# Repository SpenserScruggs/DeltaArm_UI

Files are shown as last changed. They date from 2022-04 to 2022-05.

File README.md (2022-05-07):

# DeltaArm_UI
  The goal of this project was to create a robotic arm that could track mouse movements and physically write them out on paper. Its purpose was to make signing large amounts of physical documents easier by recording a signature and then replaying it as many times as necessary. The project also exists as just a fun item to build and design and to help introduce people to robotics and electro-mechanical systems.

  This project includes the code for a graphical user interface made using WPF, Arduino code to interface with the computer, files for both the 3D printed parts and laser cut parts, MATLAB code to model the kinematic system, a bill of materials to list each part required with both their quantity and an Amazon link to purchase the part listed if applicable, and a manufacturing plan to give step by step instructions for assembly.

Final Product:


**Prototype Render:**
Untitled Project 15

**Prototype Functioning:**
https://user-images.githubusercontent.com/78044374/164074046-c8909eee-885d-474c-8c80-e7db3166021f.mov

**Record Feature:**
https://user-images.githubusercontent.com/78044374/164074614-67ea297b-0f7b-4717-87f8-4b7f0d07ca0b.mov

**MATLAB Code for Inverse Kinematics Solution:**
https://github.com/SpenserScruggs/DeltaArm_UI/blob/master/invKin.m

Code describes delta robot arms through 3 loop closure equations. Each loop closure equation is transformed from cartesian to a servo angle. Transformed loop closure equations are then trigonometrically substituted. Trig subbed equations are then solved with the quadratic formula and 2 solutions are given for every equation one solution with arms kinked in and one with arms kinked out. The kinked-out solution is selected through a sorting loop that chooses the smaller servo position thus selecting the preferred solution. From there the selected solutions from each loop closure solution is combined into an array and returned.

**AutoCAD files for frame of arm:**
https://github.com/SpenserScruggs/DeltaArm_UI/tree/master/AutoCAD%20Drawings

  Folder Contains all of the AutoCAD drawings that are needed for the frame of the arm. 

**BOM File:**
https://github.com/SpenserScruggs/DeltaArm_UI/blob/master/BOM.xlsx

  File contains all components needed for creation of the arm, as well as the prices, size, mass, and location of purchase of the components.

**Manufacturing Plan:**
https://github.com/SpenserScruggs/DeltaArm_UI/blob/master/Manufacturing%20Plan.docx

  Document provides step by step instructions for how to assemble the project.

**GUI Application:**
https://github.com/SpenserScruggs/DeltaArm_UI/tree/master/DeltaArm_UI

  This folder contains the C# and xaml code necessary to make the GUI and run the application (only works on Windows). To run it right click on the folder and select open with, then open with visual studio. Additionally if you only want the application/ don’t want to download visual studio you can download the executable directly here at: https://github.com/SpenserScruggs/DeltaArm_UI/blob/master/DeltaArm_UI.exe

**Circuit Diagram:**
https://github.com/SpenserScruggs/DeltaArm_UI/blob/master/Circuit_Diagram.png
  
  Circuit Diagram for the arduino and power supply

**Arduino Code:**
https://github.com/SpenserScruggs/DeltaArm_UI/blob/master/GUIKinematics2.ino

  Code that passes the xyz positions to the kinematic equations which can be converted to servo positions

**Source for the kinematic equations:**
https://hypertriangle.com/~alex/delta-robot-tutorial/

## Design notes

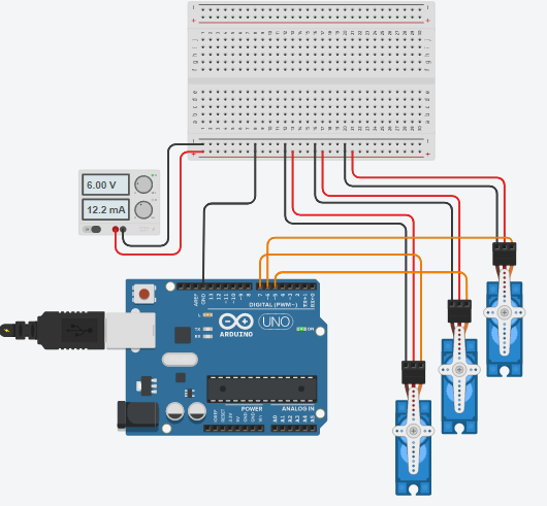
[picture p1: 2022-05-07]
Circuit_Diagram.png

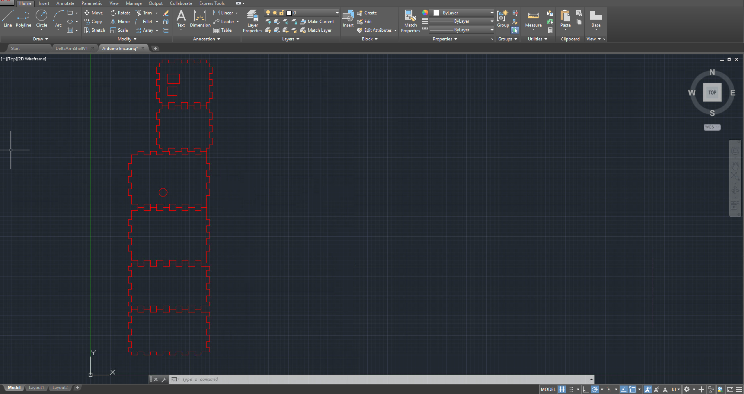
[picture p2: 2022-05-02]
AutoCAD Drawings/Arduino Casing Preview.PNG

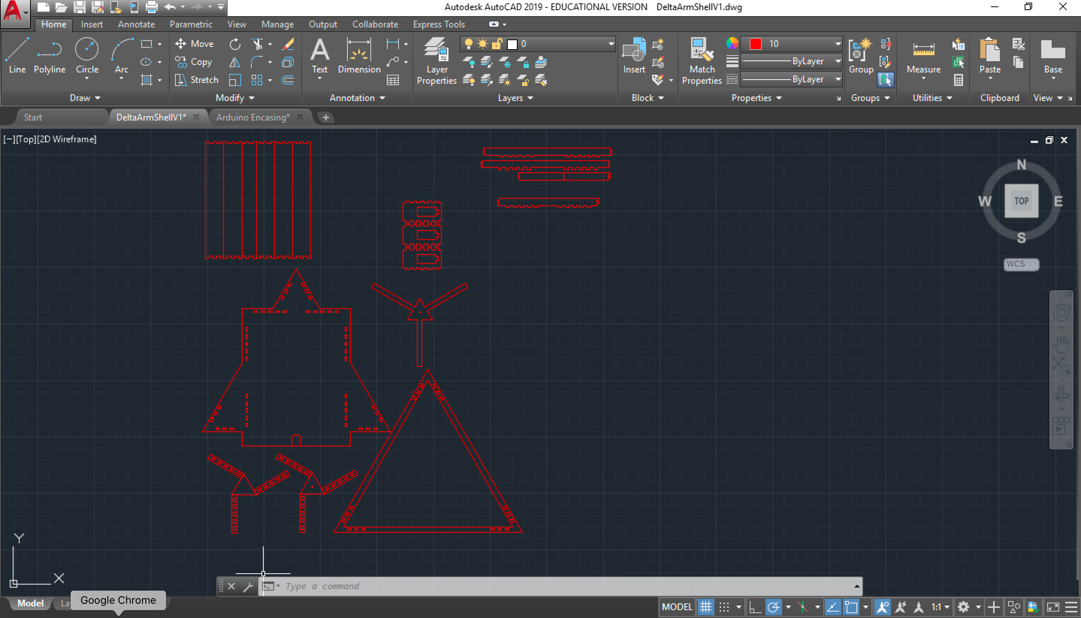
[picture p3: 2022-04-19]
AutoCAD Drawings/DeltaArmShellV1 Preview.png

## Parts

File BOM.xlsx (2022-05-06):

part_number | Part Name | Thumbnail Image | Custom Part | part_class | synopsis | revision | manufacturer_name | manufacturer_part_number | seller | link | unit_cost | Quantity | Total Cost | Mass (g) | Thickness (in)
1 | Servo Motor |  | FALSE | Servo | 180 degree servo with 12kg/cm torque | 0 | Deegoo-FPV | B07NQJ1VZ2 | Amazon | https://www.amazon.com/Control-Angle180-Digital-Torque-Helicopter/dp/B07NQJ1VZ2 | $5.50 | 3 | $16.49 | N/A | N/A
2 | Ball Joint |  | FALSE | Joint | Ball joint linkage | 0 | Uxcell | ‎A18122800ux0757 | Amazon | https://www.amazon.com/dp/B07Q2QSS72?psc=1&ref=ppx_yo2ov_dt_b_product_details | 0.9991666667 | 12 | 11.99 | N/A | N/A
3 | PSU |  | FALSE | PSU | Power supply for the servos | 0 | ‎ShenZhen ZuoEn Technologies Co. Ltd | ‎ISP-NW-PS-6V-WP-UL-12W | Amazon | https://www.amazon.com/dp/B01GCI99OG?ref=ppx_yo2ov_dt_b_product_details&th=1 | 6.29 | 1 | 6.29 | N/A | N/A
4 | Pen Pad |  | FALSE | Pen Pad | Pen control on windows computers | 0 | HUION | H430P-OTG | Amazon | https://www.amazon.com/gp/product/B078GZFY1C/ref=ppx_yo_dt_b_asin_title_o00_s00?ie=UTF8&psc=1 | 32.99 | 1 | 32.99 | N/A | N/A
5 | Lever |  | TRUE | 3D-Printed | Lever that connects servo with the arms | 1 | N/A | N/A | N/A | N/A | N/A | 3 | N/A | 6 | N/A
6 | Effector |  | TRUE | 3D-Printed | End effector that holds the pen | 2 | N/A | N/A | N/A | N/A | N/A | 1 | N/A | 3 | N/A
7 | Cap |  | TRUE | 3D-Printed | End cap for the top of the pen | 0 | N/A | N/A | N/A | N/A | N/A | 1 | N/A | 1 | N/A
8 | Lever Cap |  | TRUE | 3D-Printed | Screw cap for the lever | 0 | N/A | N/A | N/A | N/A | N/A | 6 | N/A | 1 | N/A
9 | Connector |  | TRUE | 3D-Printed | Connects the end effector with the joints | 1 | N/A | N/A | N/A | N/A | N/A | 3 | N/A | 1 | N/A
10 | Rod |  | TRUE | 3D-Printed | Connects the joints together | 1 | N/A | N/A | N/A | N/A | N/A | 6 | N/A | 4 | N/A
11 | Base Triangle |  | TRUE | Lazer-Cut | Holds the paper and side supports for arm | 0 | N/A | N/A | N/A | N/A | N/A | 1 | N/A | 900 | 1/4"
12 | TopTriangle |  | TRUE | Lazer-Cut | Holds main support for servos | 0 | N/A | N/A | N/A | N/A | N/A | 1 | N/A | 200 | 1/4"
13 | Top Support |  | TRUE | Lazer-Cut | Support for top of servos | 1 | N/A | N/A | N/A | N/A | N/A | 1 | N/A | 50 | 1/4"
14 | Bottom Support |  | TRUE | Lazer-Cut | Support for bottom of servos | 1 | N/A | N/A | N/A | N/A | N/A | 1 | N/A | 30 | 1/4"
15 | Main Support |  | TRUE | Lazer-Cut | Suspends servos above the base triangle | 0 | N/A | N/A | N/A | N/A | N/A | 1 | N/A | 30 | 1/4"
16 | Plexiglass Stands |  | TRUE | Lazer-Cut | Holds the top triangle above the base triangle | 0 | N/A | N/A | N/A | N/A | N/A | 6 | N/A | 40 | 1/8"
17 | Servo Brackets |  | TRUE | Lazer-Cut | Holds servos in place | 1 | N/A | N/A | N/A | N/A | N/A | 3 | N/A | 15 | 1/8"
18 | Arduino Box |  | TRUE | Lazer-Cut | Encloses Arduino and PCB board | 0 | N/A | N/A | N/A | N/A | N/A | 1 | N/A | 60 | 1/8"
19 | Paper Keepers |  | TRUE | Lazer-Cut | Holds paper in place on base platform | 3 | N/A | N/A | N/A | N/A | N/A | 1 | N/A | 30 | 1/8"

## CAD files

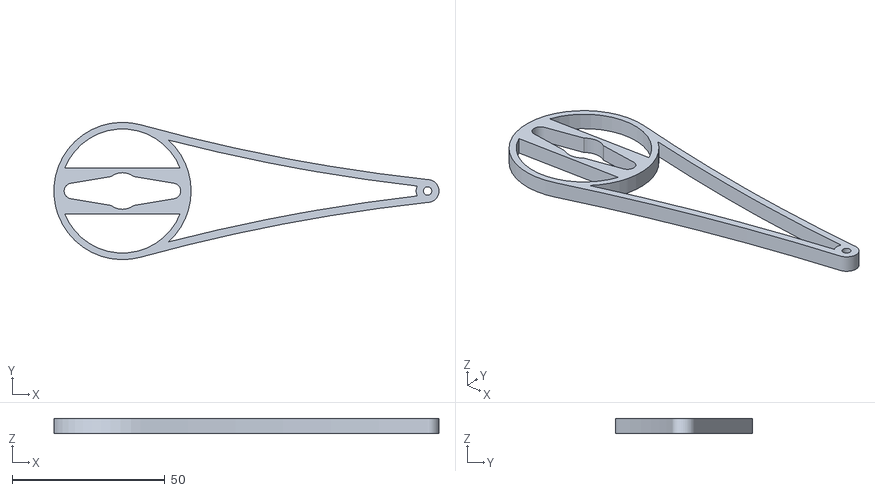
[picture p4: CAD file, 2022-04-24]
Stl_Files/lever.STL
126.2 x 45.0 x 5.00

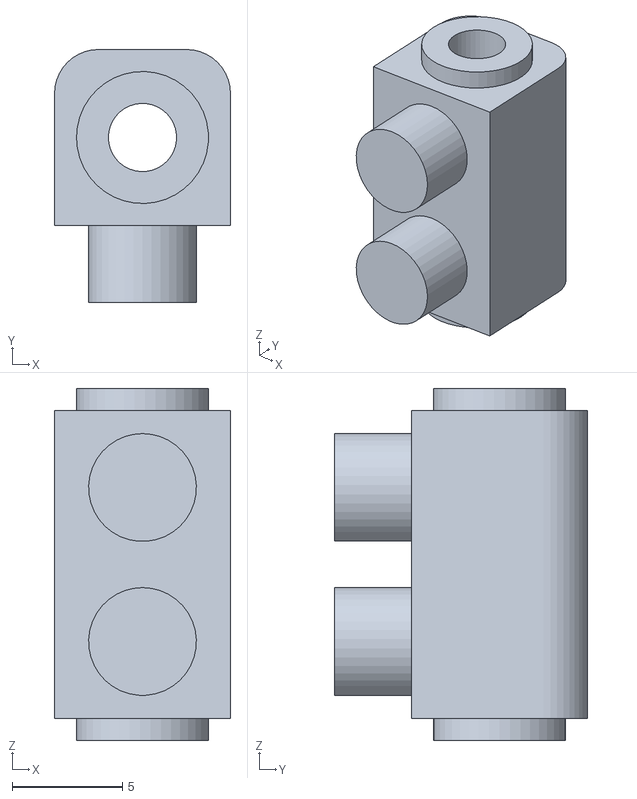
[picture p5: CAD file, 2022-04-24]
Stl_Files/connector.STL
8.00 x 11.5 x 16.0

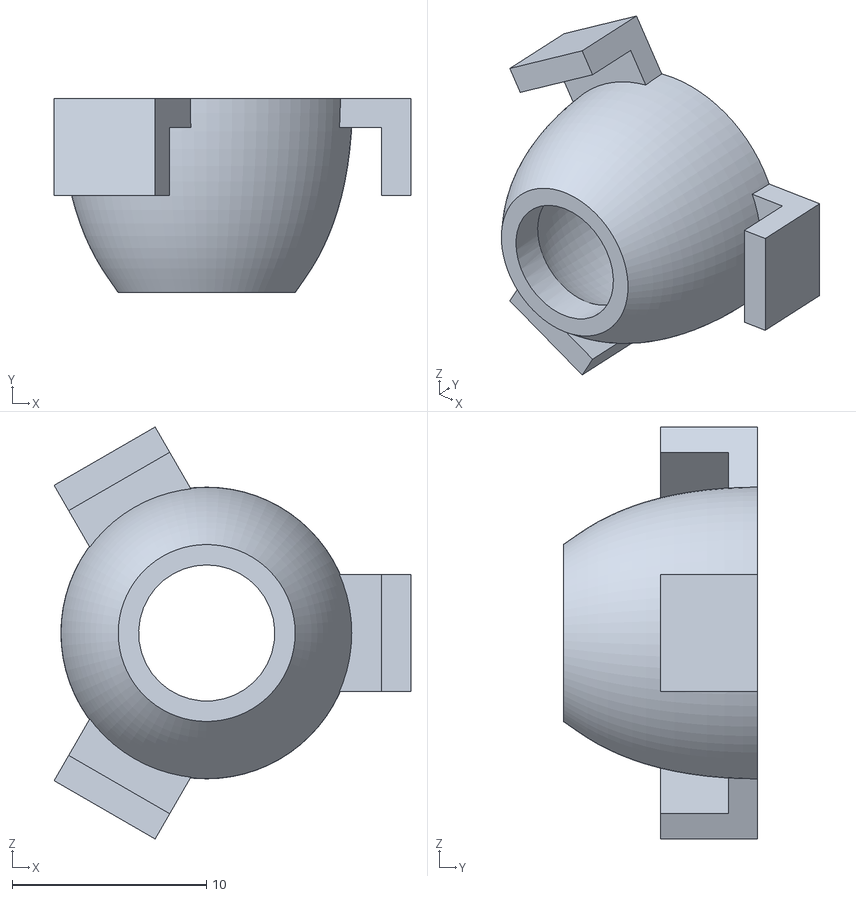
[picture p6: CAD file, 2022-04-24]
Stl_Files/cap.STL
18.3 x 10.0 x 21.2

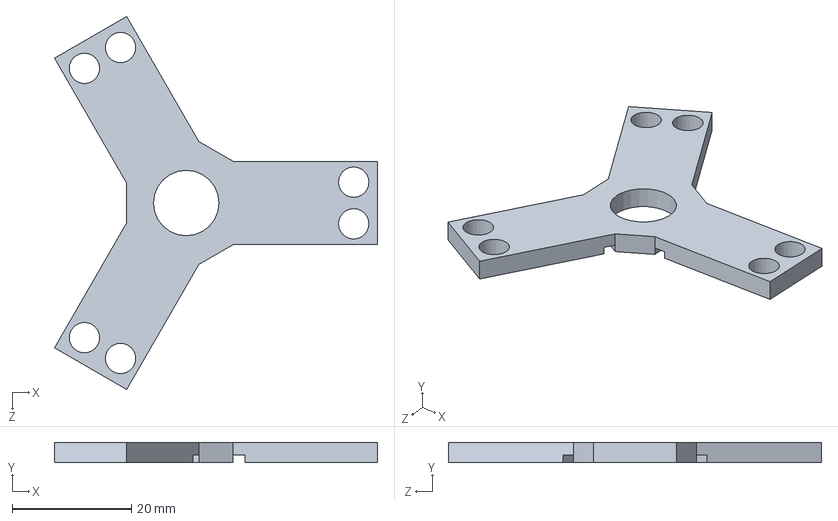
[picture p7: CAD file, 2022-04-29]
SW_Files/effector.SLDPRT
54.2 x 3.40 x 62.6 mm

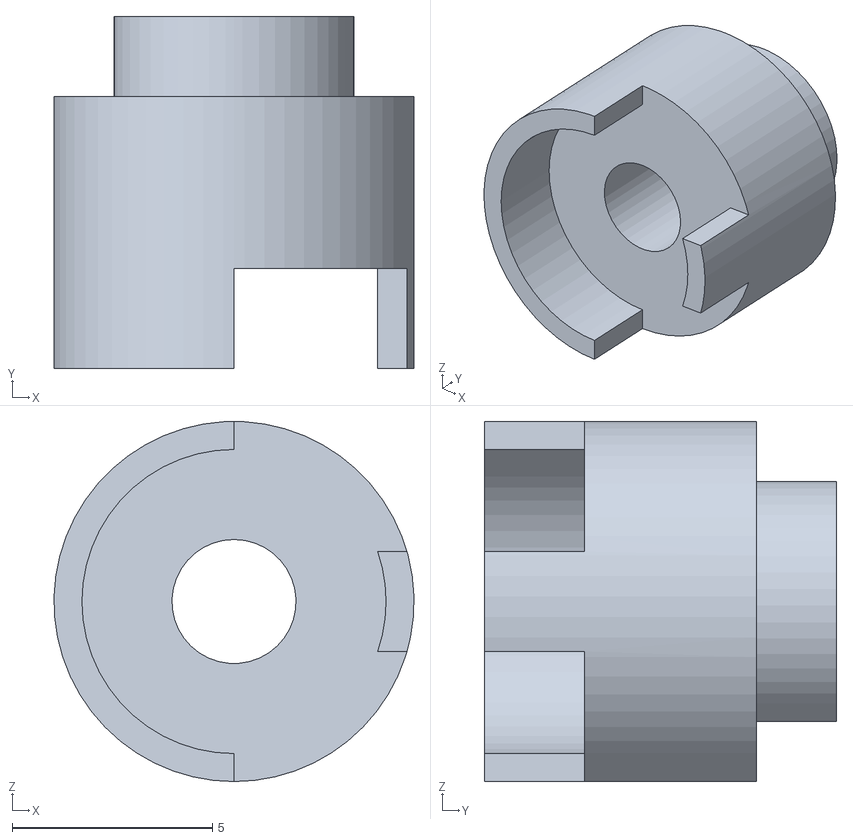
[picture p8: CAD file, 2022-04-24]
Stl_Files/endCap.STL
9.00 x 8.80 x 9.00

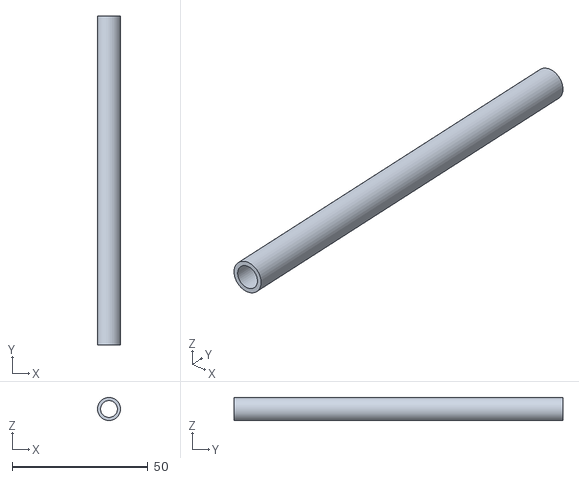
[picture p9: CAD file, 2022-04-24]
Stl_Files/stickcap.STL
8.49 x 121.0 x 8.50

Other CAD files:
AutoCAD Drawings/Arduino Encasing.dwg
SW_Files/lever.SLDPRT
AutoCAD Drawings/DeltaArmShellV1.dwg
SW_Files/connector.SLDPRT
SW_Files/Lever Cap.SLDPRT
SW_Files/cap.SLDPRT
Stl_Files/effector.STL
SW_Files/Rod.SLDPRT

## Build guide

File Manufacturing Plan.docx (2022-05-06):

Part list

1. Physical structure
  a. Base assembly
    i. Mounting/Top triangle
      1. Top triangle
      2. Main support
    ii. Base Triangle
    iii. 6 Plexiglass stands
    iv. Plexiglass paper keepers
      1. Top keepers
      2. Side keepers
      3. Bottom keepers
    v. Arduino box
  b. Servo tripod assembly
    i. 3 Servo motors
    ii. Top support
    iii. Bottom support
    iv. 3 Servo brackets
    v. 3 Levers
    vi. 3 Connectors
    vii. 3 Rods(Not finalized)
    viii. 6 Lever caps
    ix. Effector
    x. Cap
2. Electrical Connections and Circuits
  a. Arduino
  b. 3 servo motors
  c. External power source

Manufacturing plan:

1. Laser cut the following items:
  a. 1 Base Triangle
  b. 1 Top triangle
  c. 1 Main support
  d. 1 Top support
  e. 1 Bottom support
  f. The 3 servo brackets
  g. 6 Plexiglass stands
  h. Plexiglass paper keepers
  i. Arduino box
2. 3D print the following items:
  a. 3 levers
  b. 6 rods
  c. 1 Effector
  d. 3 Connectors
  e. 6 Lever caps
3. Make the servo tripod assembly
  a. Put the 3 servo brackets in the holes in the bottom support piece
    i. The servo bracket’s holes should be more outer rather than being inner facing
  b. Put the top support piece on top of the 3 servo brackets
    i. The two support pieces should be mirrored across the middle of the servo brackets
  c. Insert the servo motors into the servo brackets so the rotating part of the servo aligns with the center of the support pieces. Then hot glue the servos to the servo brackets
  d. Set the servo motors to 45 degrees each through the Arduino. Then attach the lever pieces to the servo motors so the levers are 45 degrees to the bottom support piece
  e. Use adhesive to hold the laser cut pieces together at every connection point
  f. Make the 6 rods by connecting two ball joints by their stem to the rod ends for each rod by hot glue the pieces together
  g. Put the 3 connector pieces into the holes on the effector piece. It should be just press fit but can be hot glued if necessary
  h. Connect one of the screw ends of each rod to the connector pieces on the effector. This should be press fit but can be hot glued if necessary
4. Make the base structure assembly
  a. Start with the base triangle and place the paper keepers in the holes that trace a rectangle
    i. The 2 bottom paper keepers are placed in the holes along the flat bottom of the base triangle with their flat side facing each other
    ii. The side paper keepers are placed right above the bottom paper keepers in the holes that are perpendicular to the flat bottom of the base triangle
    iii. Place the top paper keeper on top of the side paper keepers. This should close the gap between the two side keepers
  b. Place the 6 Plexiglas stands in pairs of 2 in each of the corners in the holes
  c. Place the top triangle on top of the Plexiglas stands so they fit into the holes on the top triangle
  d. Attach the main support piece to the top triangle where the 3 spokes of the main support piece are in the middle of each the top triangle’s sides
  e. Use adhesive to hold the laser cut pieces together at every connection point
5. Attach the servo tripod assembly to the main support piece by screwing the top support piece of the servo tripod to the main support piece of the base structure assembly. The central triangles of the support pieces should line up. The bottom support piece is on the same side that the lever pieces are pointed in
6. Attach the remaining screw ends and lever caps to the lever pieces where the levers and the connector pieces are parallel to the lever pieces
7. Connect the pieces of the Arduino box to each other where a box is made. The piece with a circle is the top piece. Glue together all the pieces except for the top piece. Glue the bottom piece to the top corner of the top triangle piece.
8. Electrical system
  a. Connect the ground wires of each servo (It is the brown wire on the servos) to the external power supply’s ground and the Arduino's ground
  b. Connect the power wires of each servo (It is the red wire on the servos) to the external power supply’s power
  c. Connect the signal wires of each servo (It is the orange wire on the servos) to the corresponding arduino pins. For this part, the bottom is the bottom part of the base triangle
    i. The bottom servo’s signal wire goes to the 8th digital pin on the Arduino
    ii. The right servo’s signal wire goes to the 9th digital pin on the Arduino
    iii. The left servo’s signal wire goes to the 10th digital pin on the Arduino
  d. Put the arduino into the arduino box with the serial port on the same side as the box piece with the rectangular opening. Then fit the servo wires through the top box piece’s circle.

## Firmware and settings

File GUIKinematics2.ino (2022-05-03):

#include <Servo.h>

Servo servo1, servo2, servo3;
int startpos = 45;

const float e = 25;     // end effector
const float f = 100.0;     // base
const float re = 90.0;
const float rf = 150.0;

// trigonometric constants
const float sqrt3 = 1.73205;
const float pi = 3.141592653;    // PI
const float sin120 = sqrt3 / 2.0;
const float cos120 = -0.5;
const float tan60 = sqrt3;
const float sin30 = 0.5;
const float tan30 = 1 / sqrt3;


// inverse kinematics
// helper functions, calculates angle theta1 (for YZ-pane)
int delta_calcAngleYZ(float x0, float y0, float z0, float& theta) {
    float y1 = -0.5 * 0.57735 * f; // f/2 * tg 30
    y0 -= 0.5 * 0.57735 * e;    // shift center to edge
    // z = a + b*y
    float a = (x0 * x0 + y0 * y0 + z0 * z0 + rf * rf - re * re - y1 * y1) / (2 * z0);
    float b = (y1 - y0) / z0;
    // discriminant
    float d = -(a + b * y1) * (a + b * y1) + rf * (b * b * rf + rf);
    if (d < 0) return -1; // non-existing point
    float yj = (y1 - a * b - sqrt(d)) / (b * b + 1); // choosing outer point
    float zj = a + b * yj;
    theta = 180.0 * atan(-zj / (y1 - yj)) / pi + ((yj > y1) ? 180.0 : 0.0);
    return 0;
}

// inverse kinematics: (x0, y0, z0) -> (theta1, theta2, theta3)
// returned status: 0=OK, -1=non-existing position
int delta_calcInverse(float x0, float y0, float z0, float& theta1, float& theta2, float& theta3) {
    theta1 = theta2 = theta3 = 0;
    int status = delta_calcAngleYZ(x0, y0, z0, theta1);
    if (status == 0) status = delta_calcAngleYZ(x0 * cos120 + y0 * sin120, y0 * cos120 - x0 * sin120, z0, theta2);  // rotate coords to +120 deg
    if (status == 0) status = delta_calcAngleYZ(x0 * cos120 - y0 * sin120, y0 * cos120 + x0 * sin120, z0, theta3);  // rotate coords to -120 deg
    return status;
}


void setup() {
  // put your setup code here, to run once:
  Serial.begin(115200);
  Serial.setTimeout(3);
  servo1.attach(8);
  servo2.attach(9);
  servo3.attach(10);
  
  servo1.write(startpos - 13);
  servo2.write(startpos);
  servo3.write(startpos + 9);
}

void loop() {
  while(Serial.available() == 0){
  }
  String input = Serial.readString();
  String xval, yval, zval;
  int x, y, z;
  int th1, th2, th3;
  float theta1, theta2, theta3;
  Serial.flush();

  for(int i = 0; i < 3; i++){
    xval += input[i];
    yval += input[i+3];
    zval += input[i+6]; 
  }  
  x = xval.toInt();
  y = yval.toInt();
  z = zval.toInt();
  
  x = map(x, 0, 800, -50, 50);
  y = map(y, 0, 600, -35, 35);
  
  delta_calcInverse(x, y, z, theta1, theta2, theta3);
  th1 = theta1 * -1;
  th2 = theta2 * -1;
  th3 = theta3 * -1;
  
  if((th1 && th2 && th3 > 1) && (th1 && th2 && th3 < 155)){
    servo1.write(th1 - 9);
    servo2.write(th2);
    servo3.write(th3 + 9);
  }
  input = "";
  xval, yval, zval = "";
}

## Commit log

2022-03-31 Create ArduinoCode
2022-04-04 Update ArduinoCode
2022-04-19 Create 3D Print STL files
2022-04-19 Rename 3D Print STL files to 3D_Print_STL_files
2022-04-19 Create Laser_Cut_Part_Files
